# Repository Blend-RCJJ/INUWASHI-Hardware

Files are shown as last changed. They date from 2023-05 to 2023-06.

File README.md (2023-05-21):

# INUWASHI-Hardware

アートボード 1-100

2023 Bordeaux機 「INUWASHI」のハードウェアリポジトリ

## License 諸注意

CC-BY-NC-SA 4.0

- 商用利用不可
- 継承義務
- 改変可能

現役勢の皆様はルールの**ロボットはチームメンバー自身によって製作された物でなければならない。** に抵触しないようにご注意願います。（参考にしていただく分には歓迎です👌）

## 3D Data

私たちは機体の設計にAutodesk Fusion360を使用しています。機体の最新の設計データのリンクはこちらです。ダウンロードをご希望の方はTwitterのDMにて個別にお知らせください。

[https://a360.co/41CARyh](https://a360.co/41CARyh)

## フォルダ構成

- CFRP_DXF　カーボン発注のDXFファイル
- PCB　基板データ（Autodesk Eagle）
  - 01-main　メイン基板
  - 02-UI　UI基板
  - 03-ToF　距離センサ基板
  - 04-bottom　下段基板
  - 05-PWR　電源基板

## Topic

最近近くの伊吹山でいぬわしのひなが生まれたらしいです。ぴよぴよかわいいね！！

無題 - 2023年5月15日 22 13

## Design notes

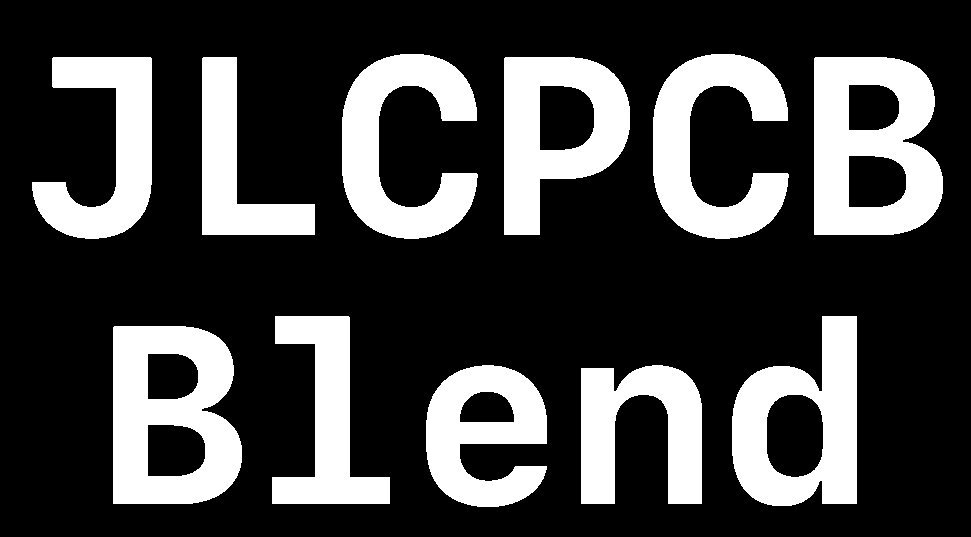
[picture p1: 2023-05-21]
PCB/03-ToF/top.bmp

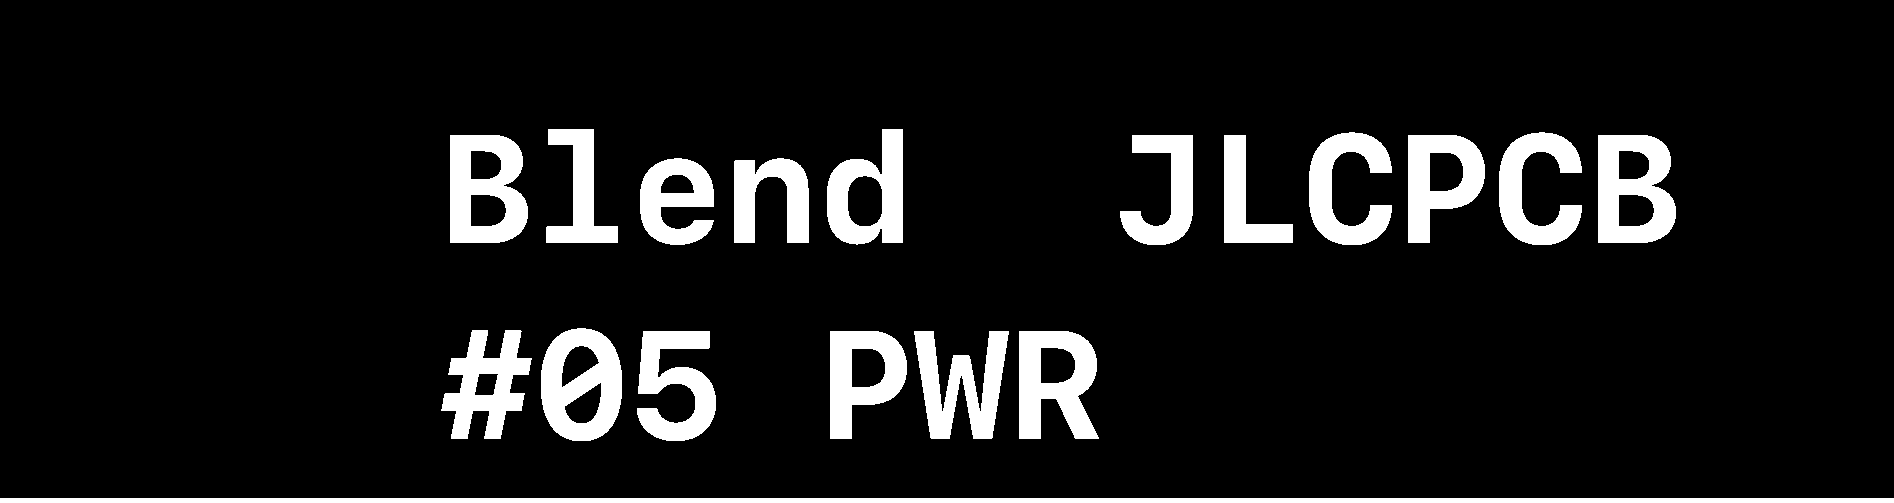
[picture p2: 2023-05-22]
PCB/05-PWR/アセット 2@5x.bmp

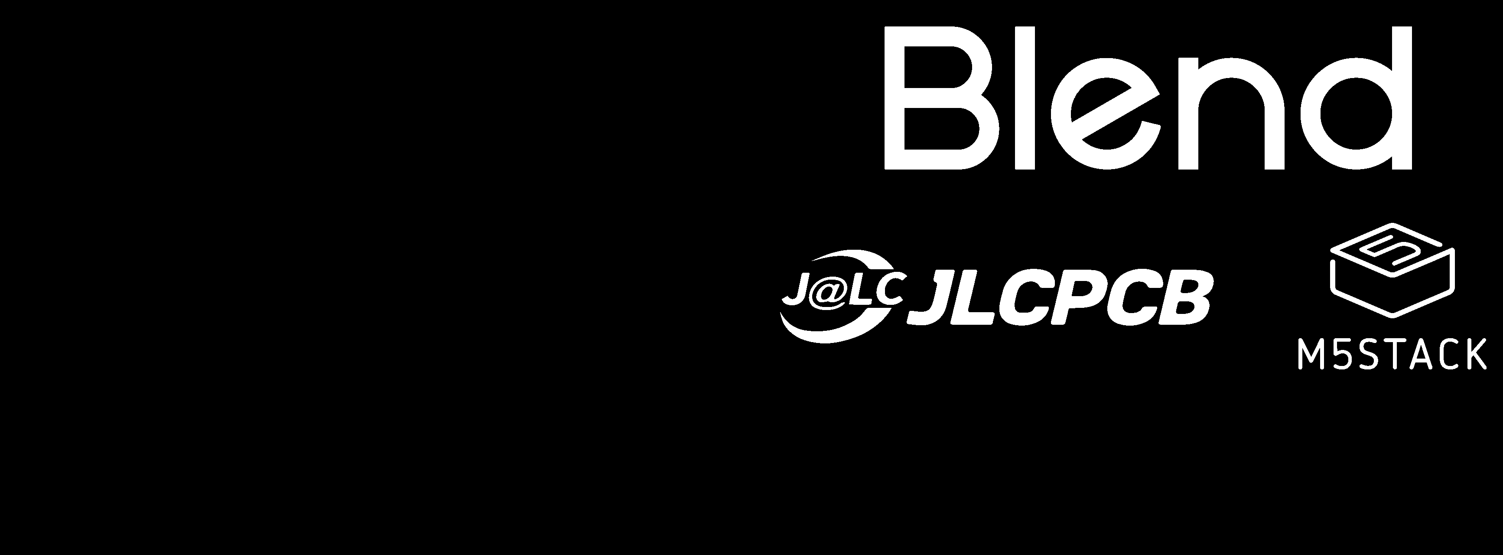
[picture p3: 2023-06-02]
PCB/01-main/アートボード 2@5x.bmp

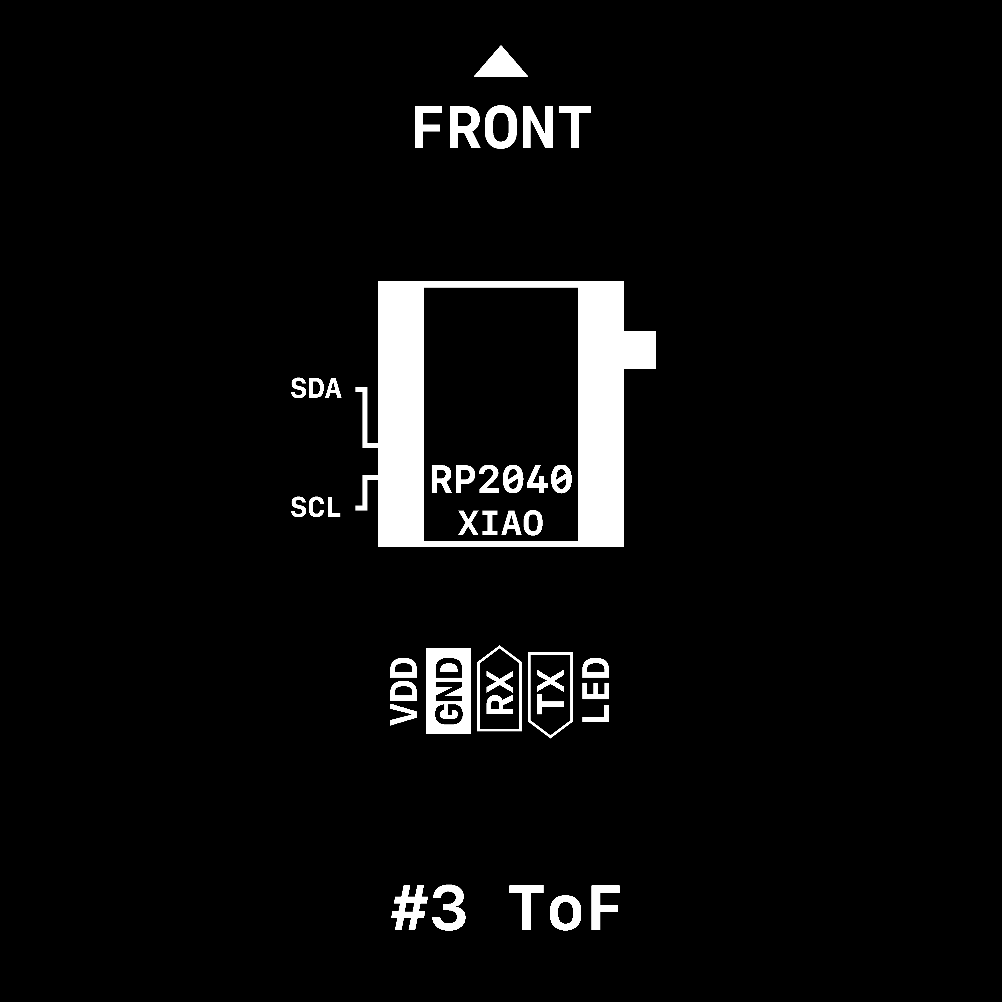
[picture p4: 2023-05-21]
PCB/03-ToF/bottom.bmp

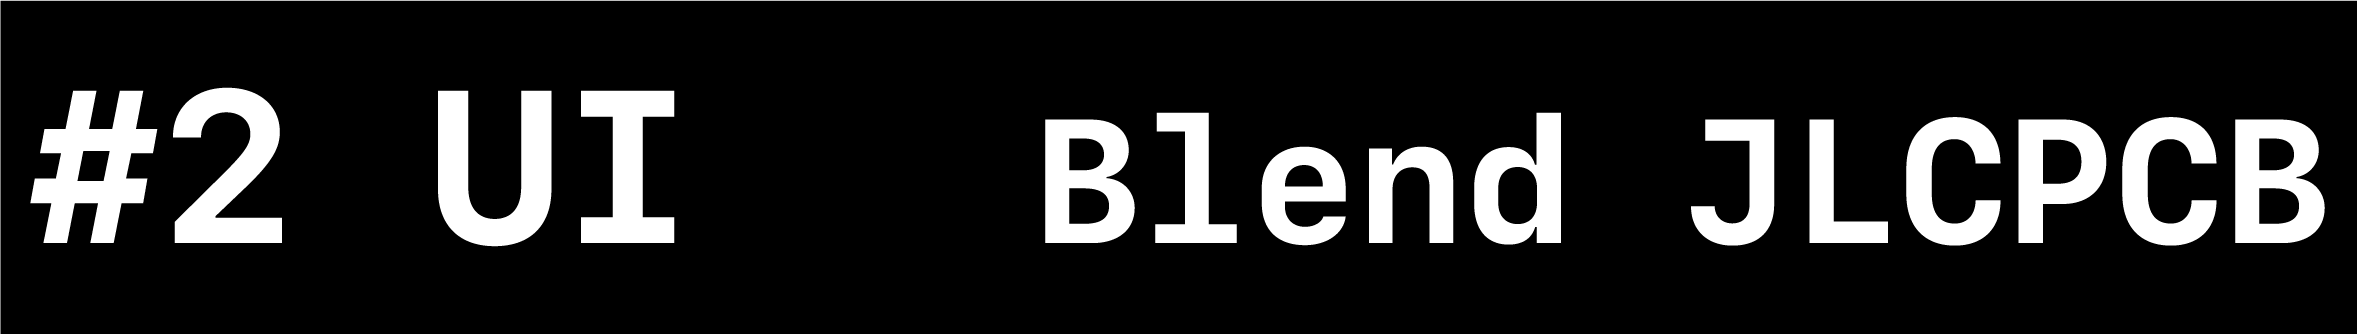
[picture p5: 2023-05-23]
PCB/02-UI/アセット 1@5x.png

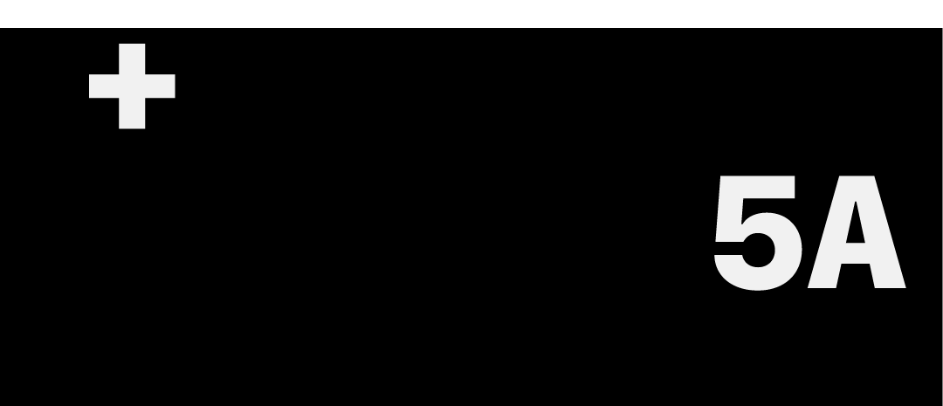
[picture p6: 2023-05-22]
PCB/05-PWR/アセット 1@5x.png

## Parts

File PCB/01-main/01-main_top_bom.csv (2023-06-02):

Comment | Designator | Footprint | LCSC Part #
0.1µ | C2 C3 C4 C5 C6 C7 C11 C14 C16 C18 | C0603 | C14663
1N4001 | D1 D2 D4 | SMA-DO214AC | C727079
1µ | C8 C17 C19 | C0603 | C15849
2k2 | R15 R16 | R0402 | C25879
4.7µ | C1 | C0603 | C19666
5k1 | R1 R2 | R0402 | C25879
7.5k | R17 | R0402 | C25918
10k | R4 R12 R13 R30 R31 | R0402 | C25744
20k | R14 | R0402 | C25765
100μ | C9 C13 C20 | 153CLV-0505 | C72487
270 | R3 R10 R32 | R0402 | C25099
BLUE | LED15 | SML0603 | C118339
BSS138 | T1 | SOT-23 | C112239
C1015 | Q1 | SOT23 | C181170
CH340ESMD | U1 | MSOP10 | C99652
MAX485ESA+T | U5 | SOIC127P600X175-8N | MAX485ED
MLT-8530 | LS1 | MLT-8530_JHE | C94599
STM32F446RET6 | U2 | LQFP64-10X10MM | C69336
WHITE | LED17 LED18 | SML0603 | C389521
WS2812B_2020 | LED1 LED2 LED3 LED4 LED5 LED6 LED7 LED8 LED9 LED10 LED11 LED12 LED13 LED14 | WS2812B_2020 | C965555
usb-c | X2 | USB_C_CUSB31-CFM2AX-01-X | C2987386

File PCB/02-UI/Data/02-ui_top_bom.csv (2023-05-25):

Comment | Designator | Footprint | LCSC Part #
WS2812B_2020 | LED1 LED2 LED3 LED4 LED5 LED6 LED7 LED8 LED9 LED10 LED11 LED12 LED13 LED14 | WS2812B_2020 | C965555

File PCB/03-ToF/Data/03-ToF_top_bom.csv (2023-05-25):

Comment | Designator | Footprint | LCSC Part #
0.1μ | C1 | C0402 | C285034
1N4007 | D1 | SMA-DO214AC | C727081
180 | R3 R4 | R0402 | C38941
1μ | C2 | C0402 | C52923
10k | R1 R2 R5 R6 R7 R8 R9 R10 R11 R12 R13 R14 R15 R16 R17 R18 R19 R20 R21 | R0402 | C269674
100μ | C3 C4 | 153CLV-0505 | C269674
BLUE | LED40 LED41 | SML0603 | C118339
NJM7805 | REG1 | MYPARTS_D-PAK_TO252AA
PCA9555PW 112 | U2 | SOP65P640X110-24N | C128392
WS2812B_5050N | LED1 LED2 LED3 LED4 LED5 LED6 LED7 LED8 LED9 LED10 LED11 LED12 LED13 LED14 LED15 LED16 LED17 LED18 LED19 LED20 LED21 LED22 LED23 LED24 LED25 LED26 LED27 LED28 LED29 LED30 LED31 LED32 | WS2812B-NARROW | C2874885

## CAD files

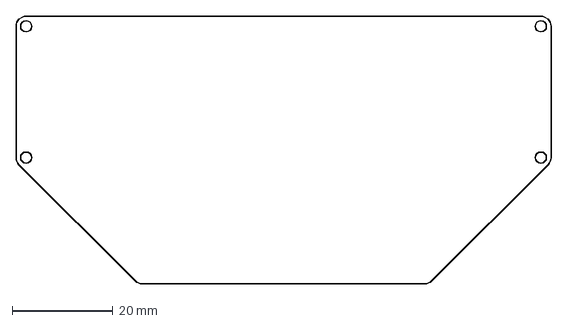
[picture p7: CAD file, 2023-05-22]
PCB/01-main/main.dxf
106.0 x 53.0 mm

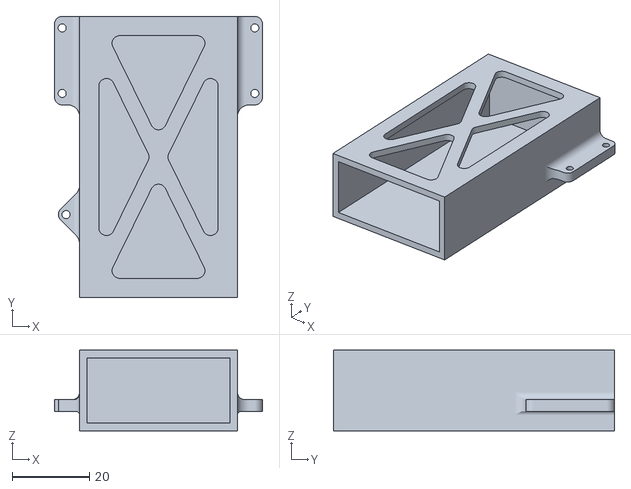
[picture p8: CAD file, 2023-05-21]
3D-Print/07-Battery-B-x4.stl
54.0 x 73.0 x 21.0

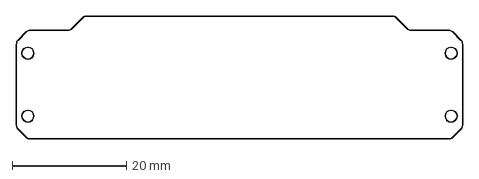
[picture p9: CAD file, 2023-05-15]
CFRP_DXF/02-patapata.dxf
78.0 x 21.5 mm

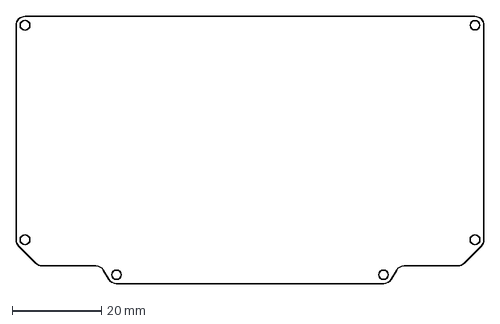
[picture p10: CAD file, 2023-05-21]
PCB/02-UI/02-ui.dxf
105.0 x 60.0 mm

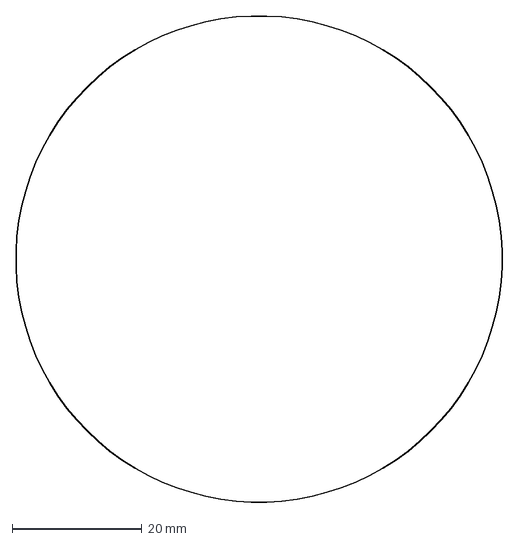
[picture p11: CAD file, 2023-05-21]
PCB/03-ToF/beta.dxf
75.0 x 75.0 mm

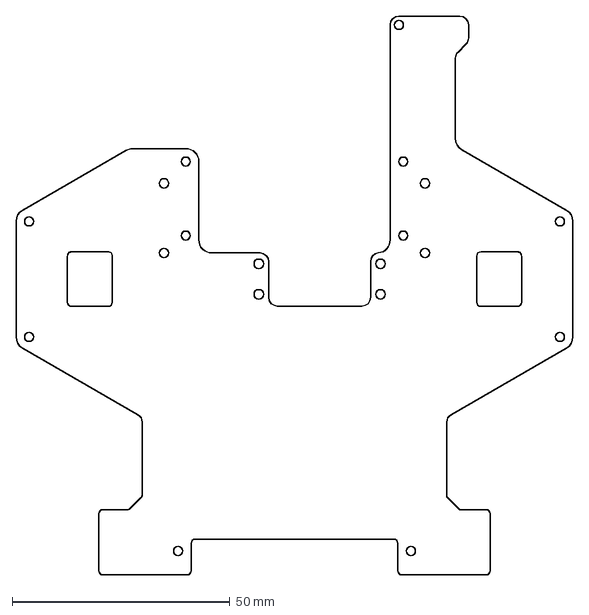
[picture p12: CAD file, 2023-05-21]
PCB/04-manta/04-bottom.dxf
128.0 x 128.5 mm

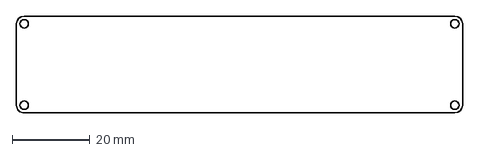
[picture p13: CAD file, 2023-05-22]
PCB/05-PWR/003-UI.dxf
115.0 x 25.0 mm

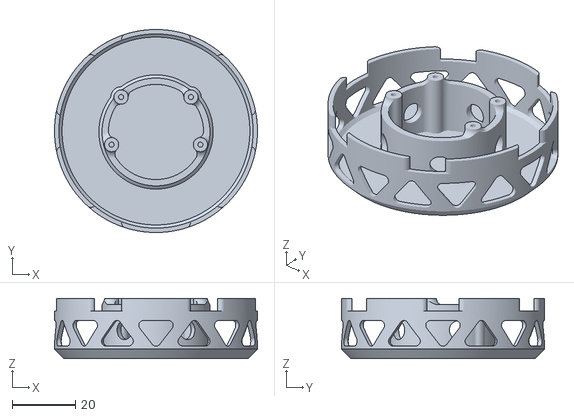
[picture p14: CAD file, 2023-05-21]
3D-Print/04-ToF-x3.stl
64.0 x 64.0 x 19.0

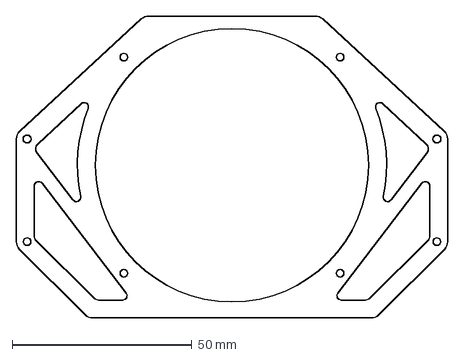
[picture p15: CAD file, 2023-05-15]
CFRP_DXF/01-top.dxf
120.0 x 84.0 mm

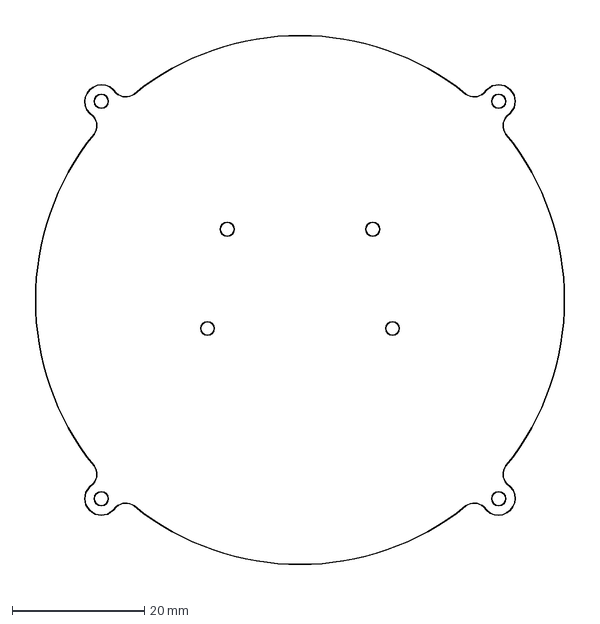
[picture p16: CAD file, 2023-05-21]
PCB/03-ToF/tof.dxf
85.9 x 85.9 mm

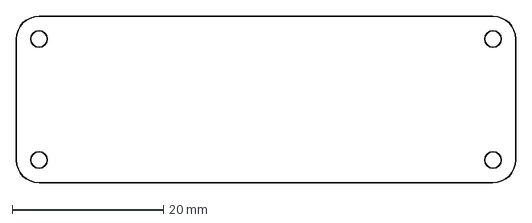
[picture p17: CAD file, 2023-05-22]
PCB/05-PWR/pwr.dxf
66.0 x 22.0 mm

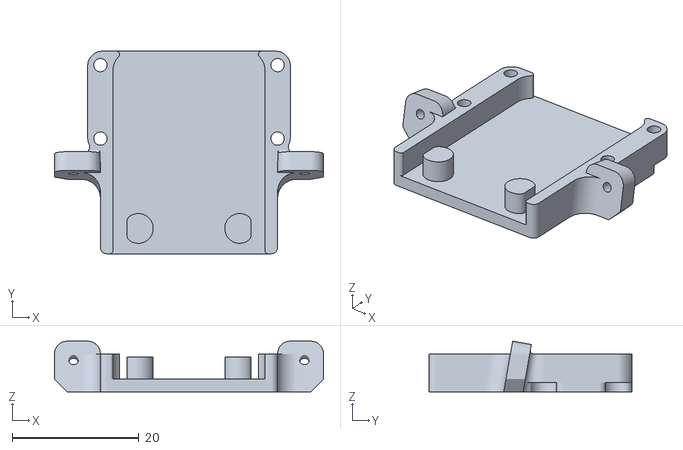
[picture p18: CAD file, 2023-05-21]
3D-Print/05-Camera-B-x6.stl
42.5 x 32.0 x 8.00

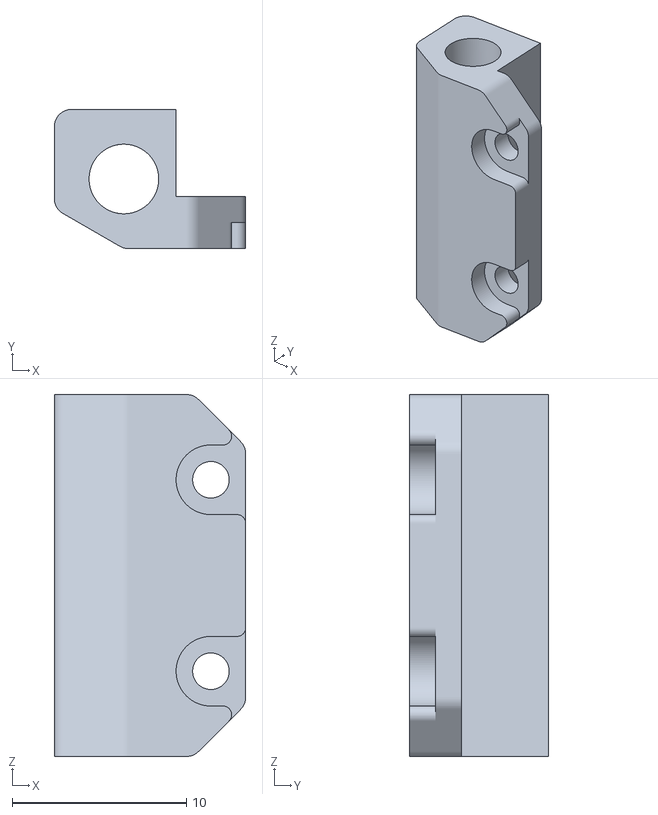
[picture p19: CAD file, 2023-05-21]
3D-Print/10-patapata-x4.stl
11.0 x 8.00 x 20.8

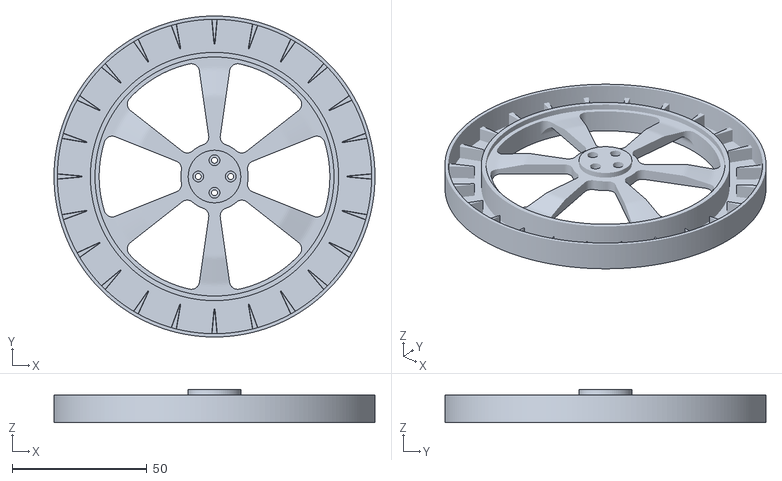
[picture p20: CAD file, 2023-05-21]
3D-Print/08-guruguru-x3.stl
119.0 x 119.0 x 12.3

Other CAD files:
3D-Print/06-Battery-A-x4.stl
3D-Print/02-Futa-A-x10.stl
3D-Print/04-Camera-A-x6.stl
3D-Print/08-guruguru-rev.2-x3.stl
3D-Print/01-Futa-B-x10.stl
3D-Print/09-gear-10.stl
3D-Print/09-gear-x10.stl

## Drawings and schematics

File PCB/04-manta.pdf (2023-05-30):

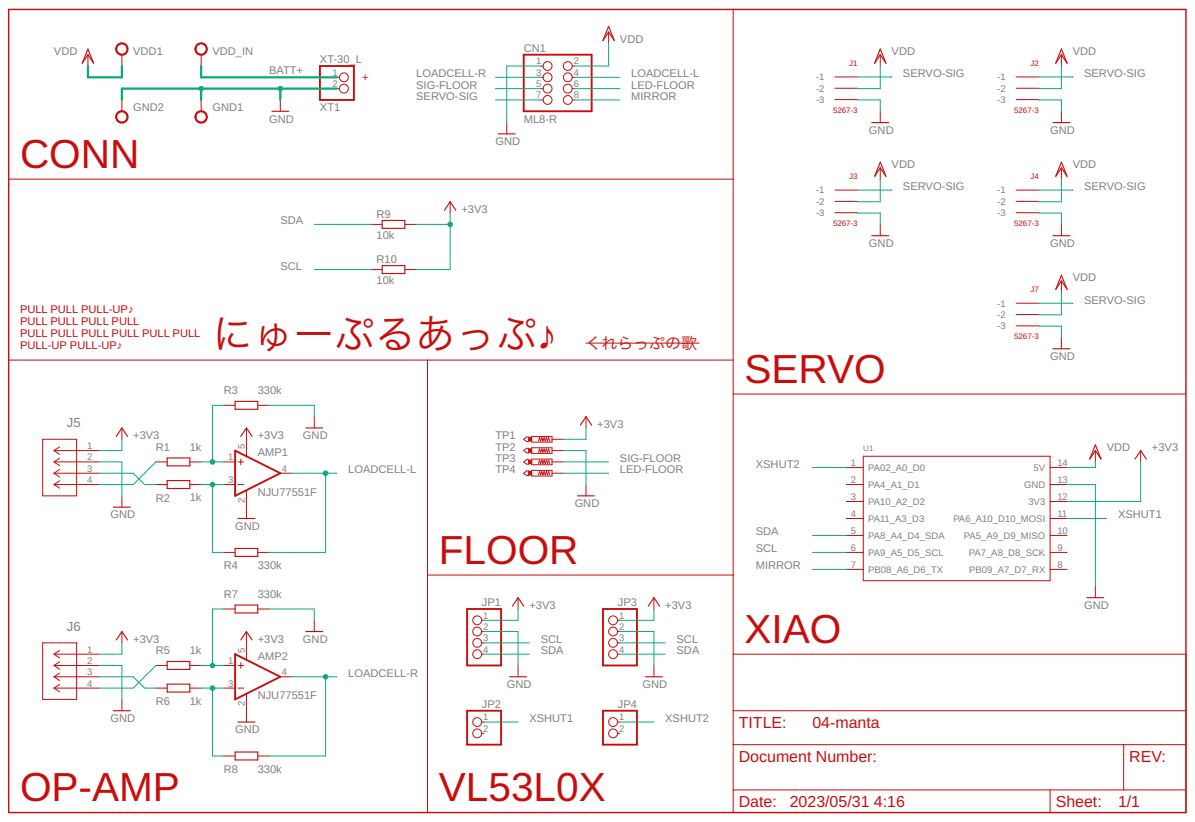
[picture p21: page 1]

CONN

PULL PULL PULL-UP♪ PULL PULL PULL PULL PULL PULL PULL PULL PULL PULL PULL-UP PULL-UP♪ | | くれらっぷの歌

R3 330k | TP2 GND FLOOR

Document Number: | REV:

Date: 2023/05/31 4:16 | Sheet: 1/1

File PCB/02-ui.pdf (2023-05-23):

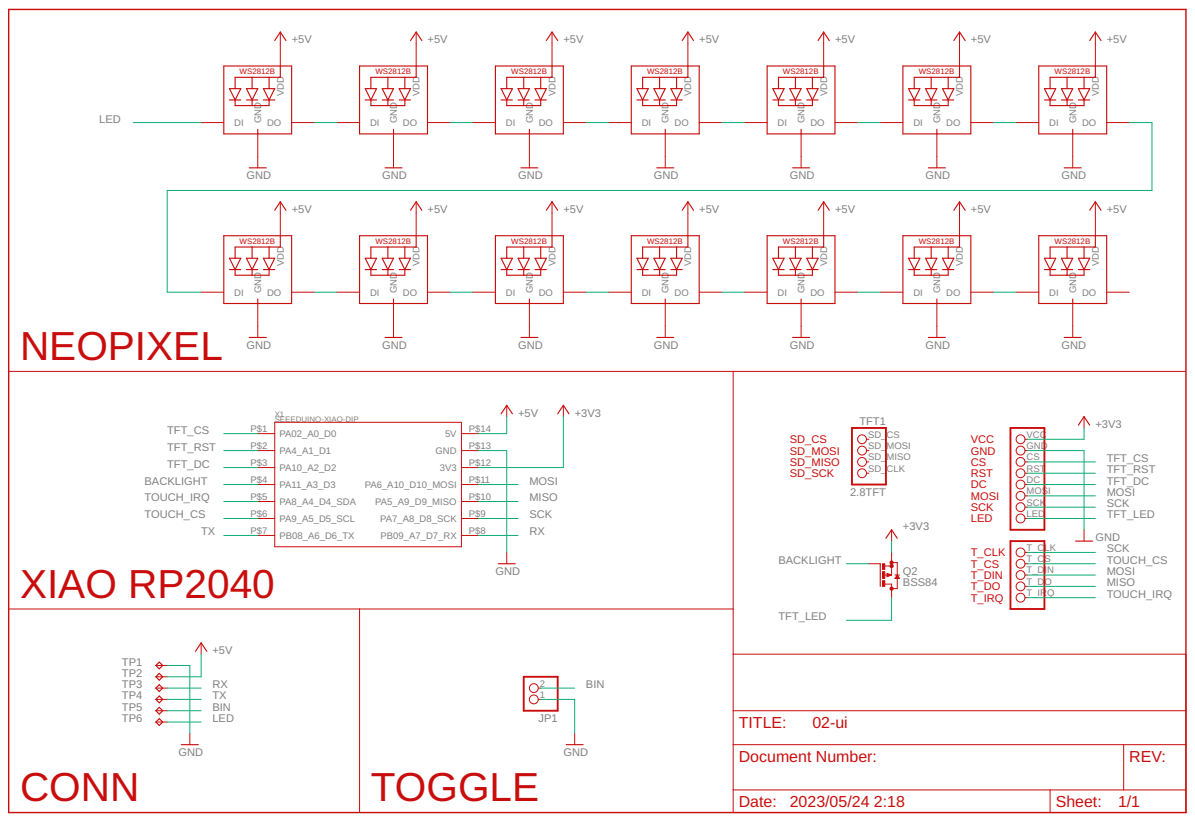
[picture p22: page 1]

XIAO RP2040 | GND

GND

Document Number: | REV:

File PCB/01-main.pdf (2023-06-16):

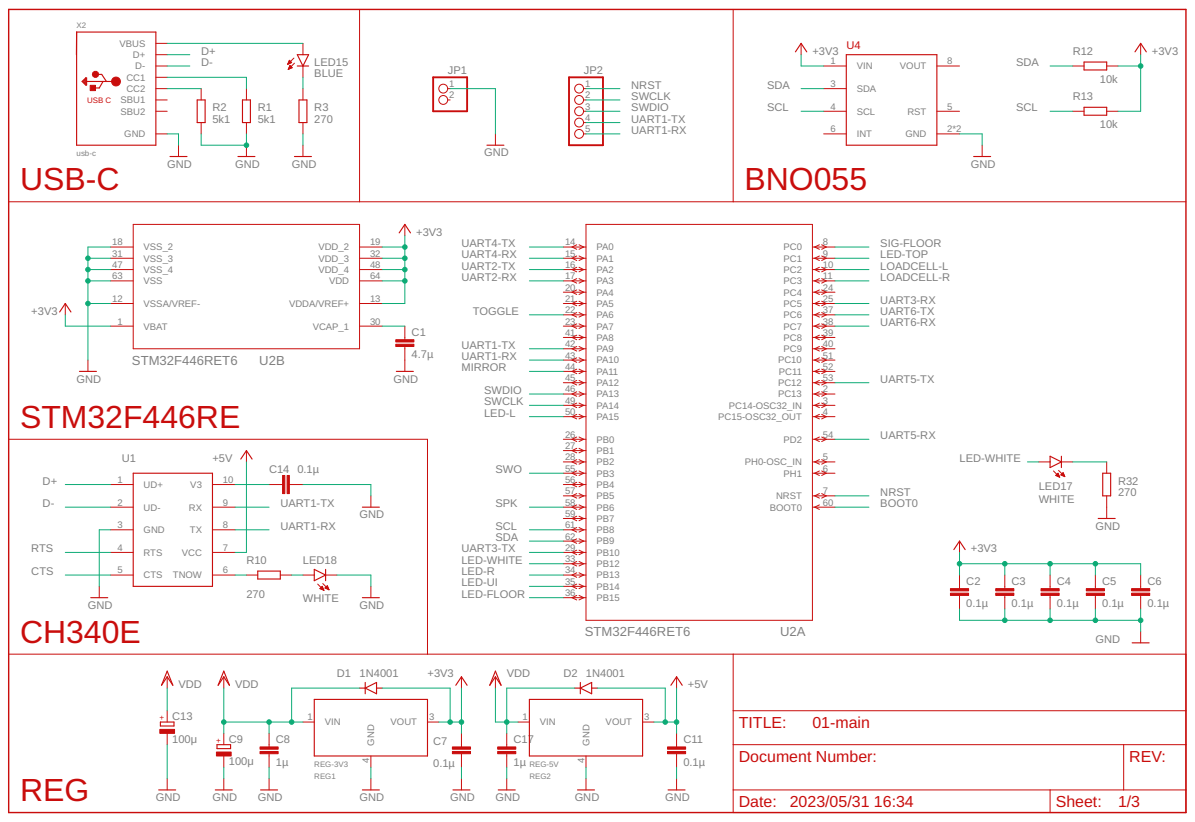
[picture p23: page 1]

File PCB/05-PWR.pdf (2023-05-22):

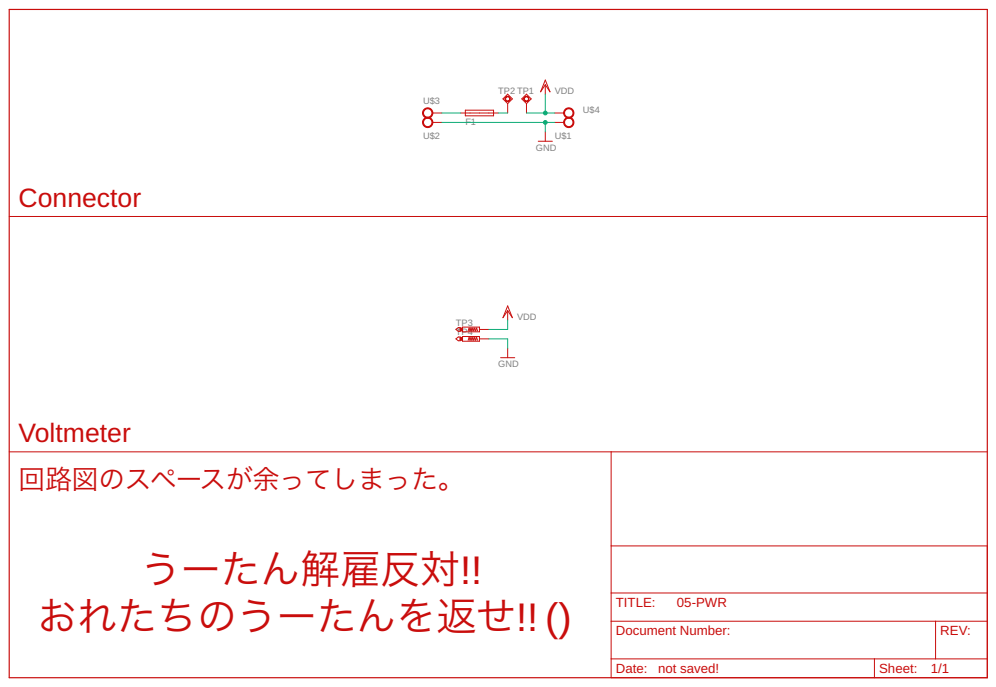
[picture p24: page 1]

回路図のスペースが余ってしまった。 うーたん解雇反対!! おれたちのうーたんを返せ!! ()

Document Number: | REV:

Date: not saved! | Sheet: 1/1

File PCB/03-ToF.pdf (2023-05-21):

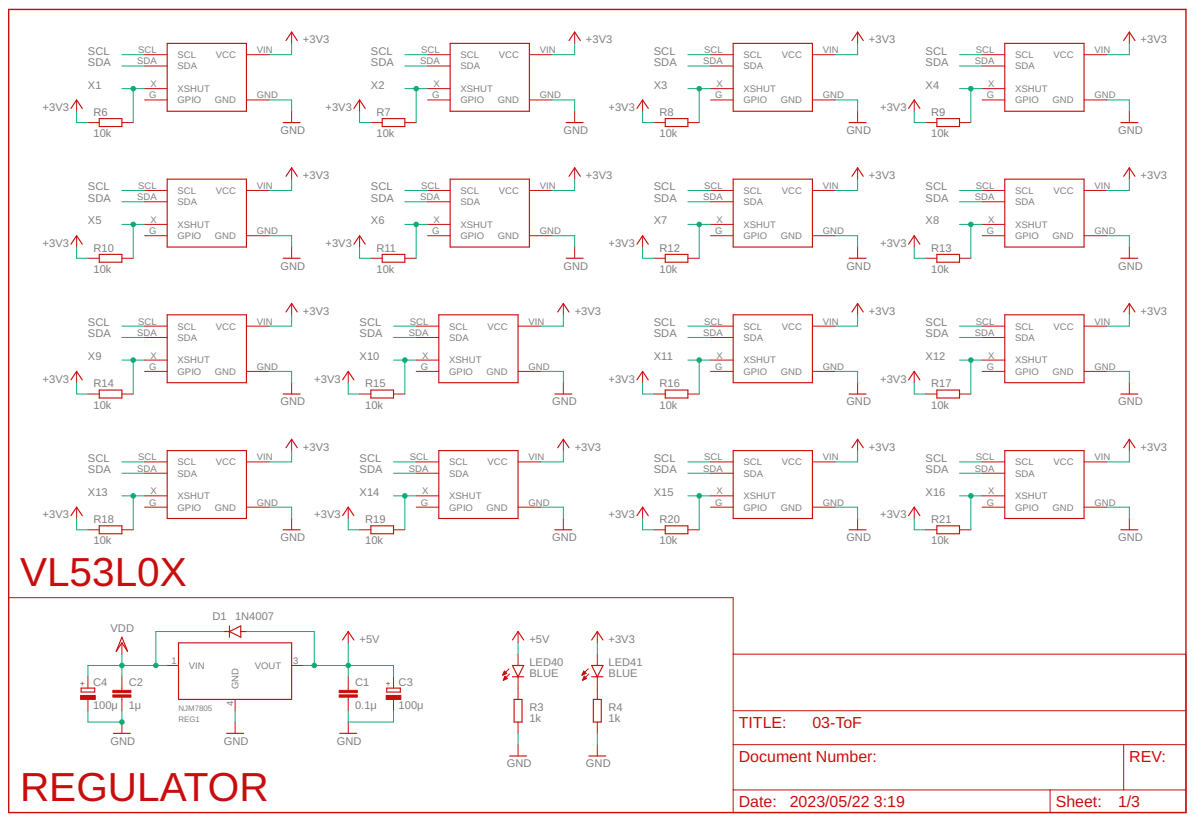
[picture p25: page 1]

Document Number: | REV:

Date: 2023/05/22 3:19 | Sheet: 1/3

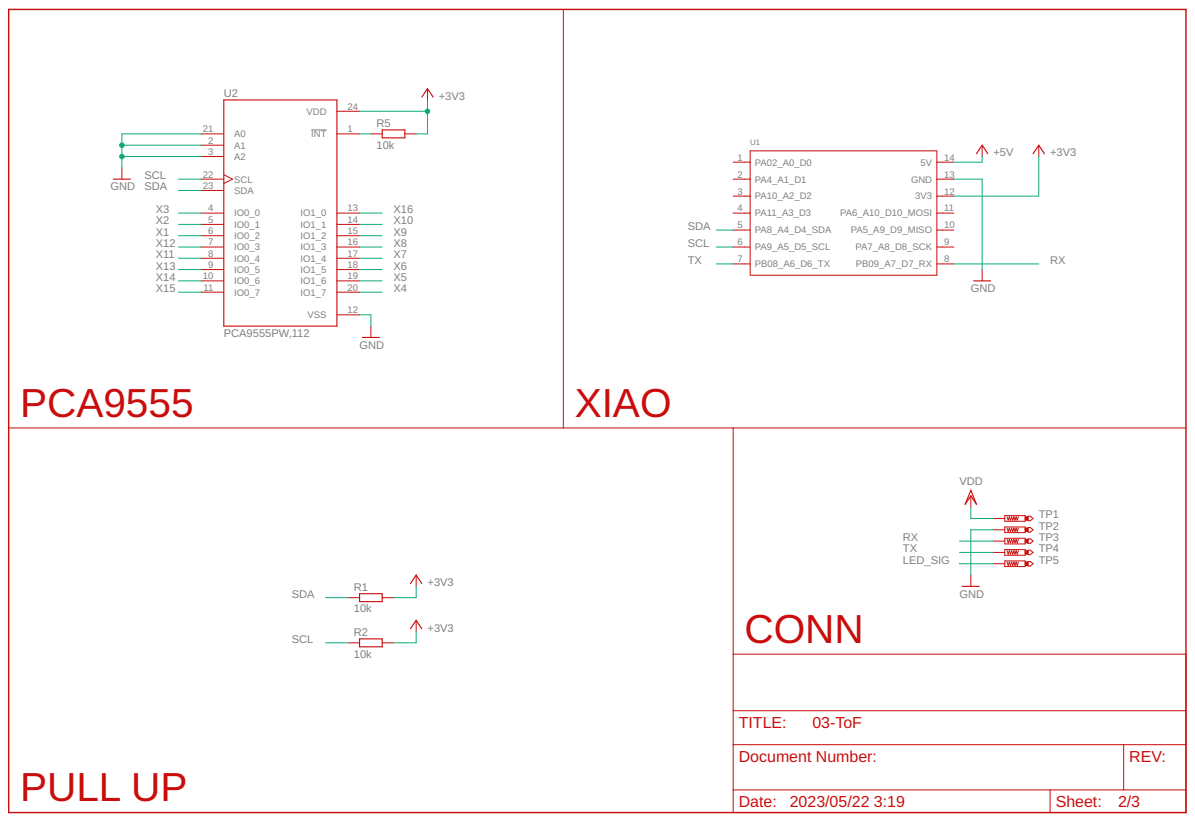
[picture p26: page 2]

Document Number: | REV:

Date: 2023/05/22 3:19 | Sheet: 2/3

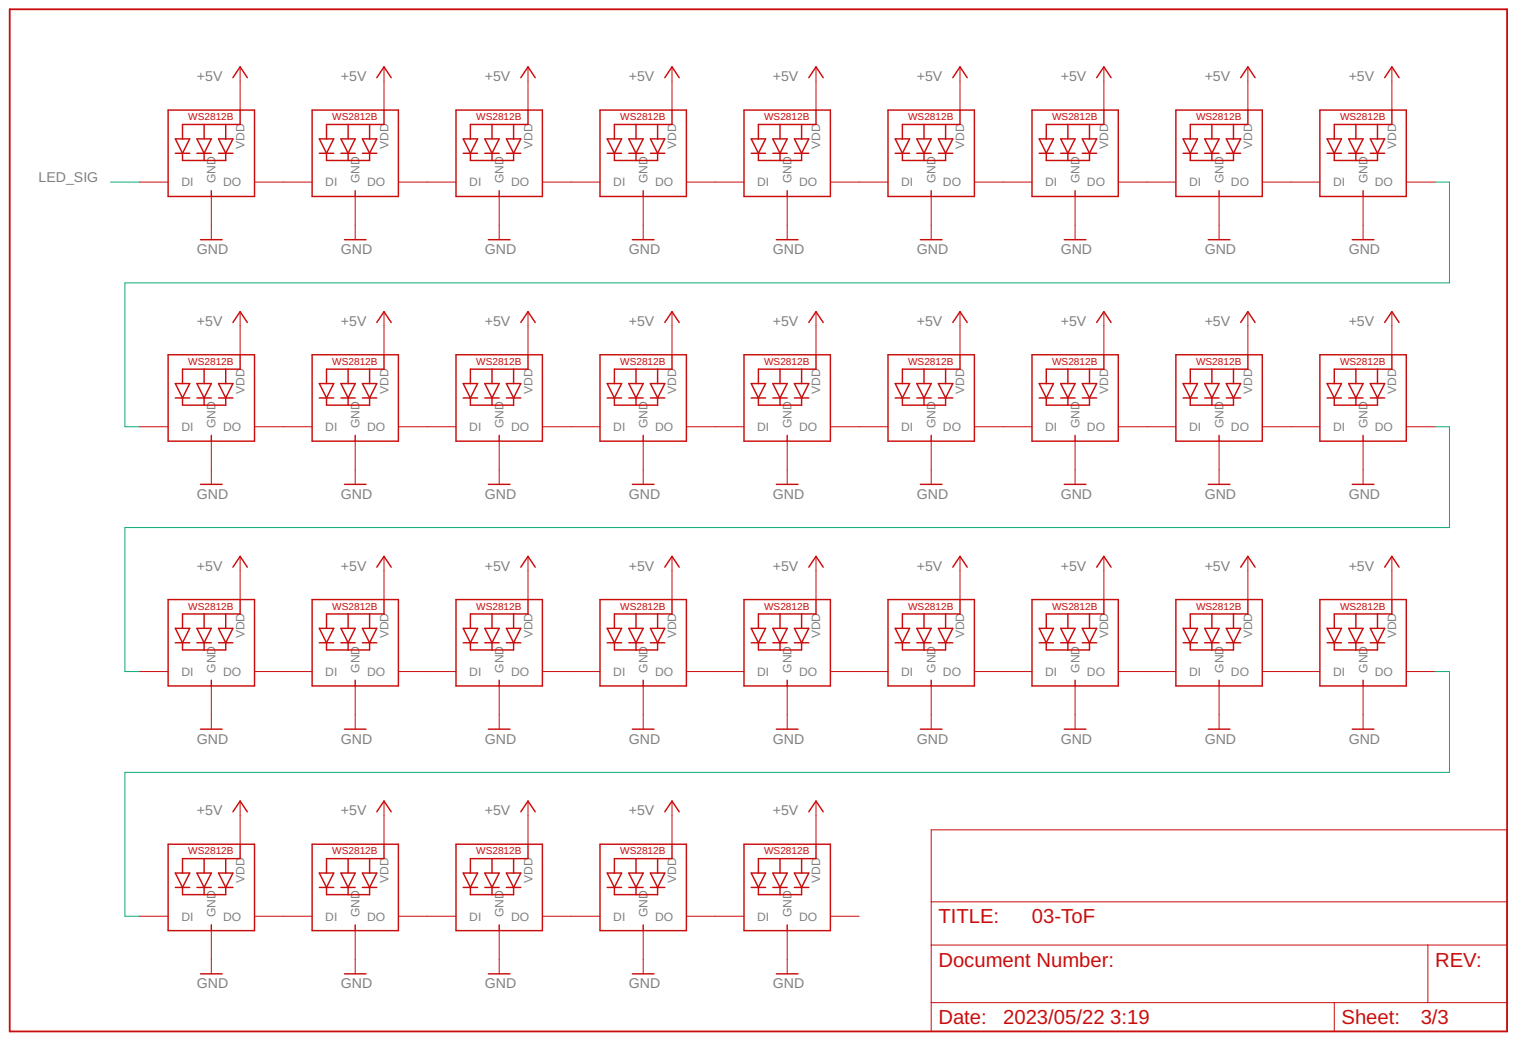
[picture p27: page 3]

Document Number: | REV:

Date: 2023/05/22 3:19 | Sheet: 3/3

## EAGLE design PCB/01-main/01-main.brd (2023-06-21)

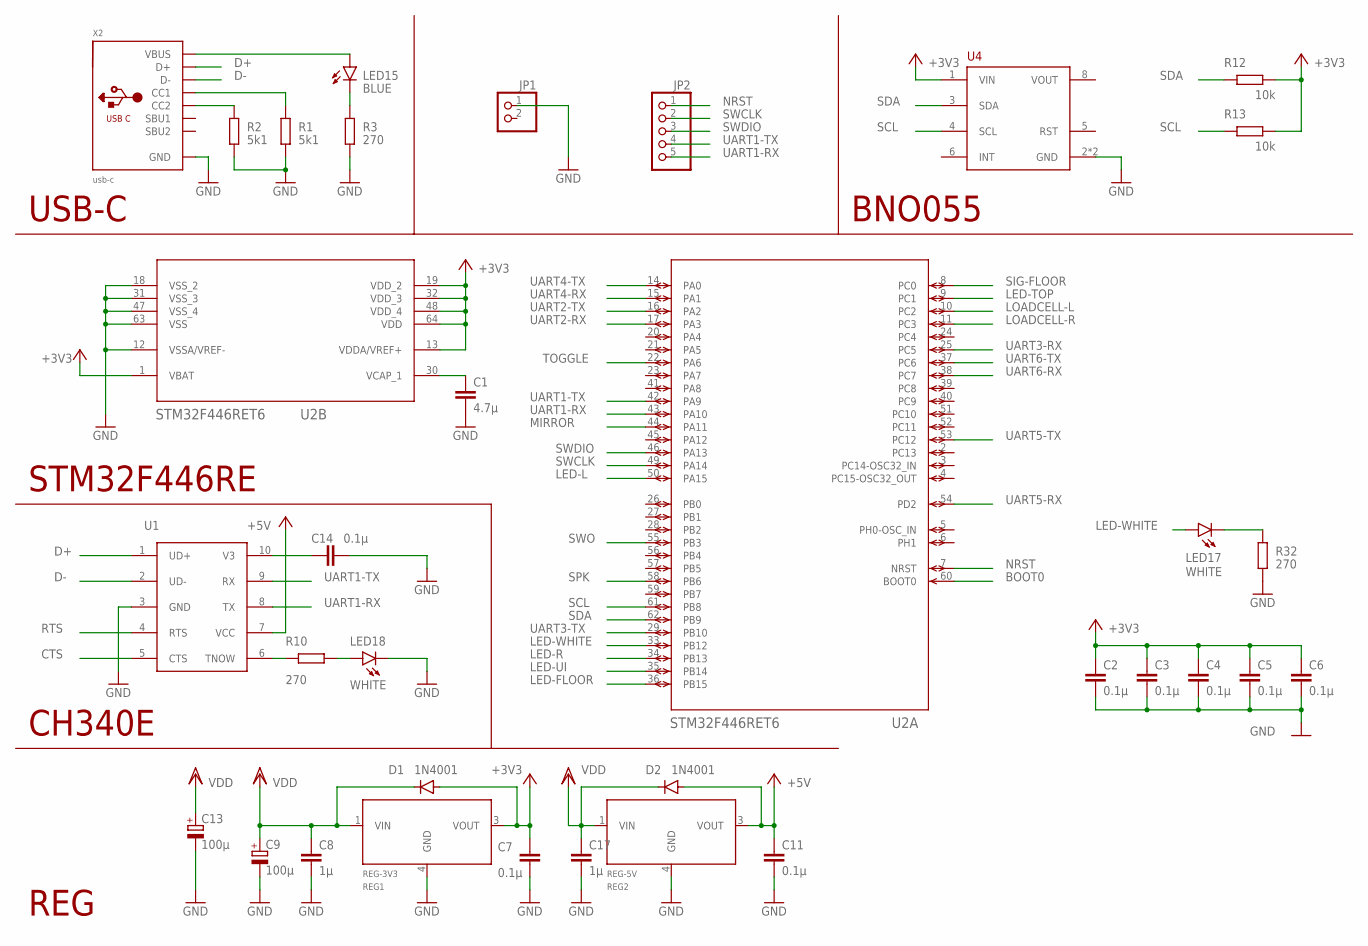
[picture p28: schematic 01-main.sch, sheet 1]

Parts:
C1: 4.7µ; C0603
C2, C3, C4, C5, C6, C7, C11, C14: 0.1µ; C0603
C8, C17: 1µ; C0603
C9, C13: 100μ; 153CLV-0505
D1, D2: 1N4001; SMA-DO214AC
JP1: PINHD-1X2; 1X02
JP2: PINHD-1X5; 1X05
LED15: BLUE; SML0603
LED17, LED18: WHITE; SML0603
R1, R2: 5k1; R0402
R3, R10, R32: 270; R0402
R12, R13: 10k; R0402
REG1: REG-3V3; MYPARTS_D-PAK_TO252AA
REG2: REG-5V; MYPARTS_D-PAK_TO252AA
U1: CH340ESMD; MSOP10
U2: STM32F446RET6; LQFP64-10X10MM
U4: BNO055; SOCKET-08
X2: usb-c; USB_C_CUSB31-CFM2AX-01-X

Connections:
+3V3: C2.1, C3.1, C4.1, C5.1, C6.1, C7.1, D1.A, R12.1, R13.1, REG1.3 (VOUT), U2.1 (VBAT), U2.13 (VDDA/VREF+), U2.19 (VDD_2), U2.32 (VDD_3), U2.48 (VDD_4), U2.64 (VDD), U4.1 (VIN); also elsewhere on the board
+5V: C11.1, D2.A, REG2.3 (VOUT), U1.7 (VCC); also elsewhere on the board
BOOT0: U2.60 (BOOT0); also elsewhere on the board
CTS: U1.5 (CTS)
D+: U1.1 (UD+), X2.A6 (D+), X2.B6 (D+)
D-: U1.2 (UD-), X2.A7 (D-), X2.B7 (D-)
GND: C1.2, C2.2, C3.2, C4.2, C5.2, C6.2, C7.2, C8.2, C9.-, C11.2, C13.-, C14.2, C17.2, JP1.1, LED18.C, R1.2, R2.2, R3.1, R32.1, REG1.4 (GND), REG2.4 (GND), U1.3 (GND), U2.12 (VSSA/VREF-), U2.18 (VSS_2), U2.31 (VSS_3), U2.47 (VSS_4), U2.63 (VSS), U4.2 (GND), U4.7 (GND), X2.A1B12 (GND), X2.B1A12 (GND); also elsewhere on the board
LED-FLOOR: U2.36 (PB15); also elsewhere on the board
LED-L: U2.50 (PA15); also elsewhere on the board
LED-R: U2.34 (PB13); also elsewhere on the board
LED-TOP: U2.9 (PC1); also elsewhere on the board
LED-UI: U2.35 (PB14); also elsewhere on the board
LED-WHITE: LED17.A, U2.33 (PB12)
LOADCELL-L: U2.10 (PC2); also elsewhere on the board
LOADCELL-R: U2.11 (PC3); also elsewhere on the board
MIRROR: U2.44 (PA11); also elsewhere on the board
unnamed: C14.1, U1.10 (V3)
unnamed: R1.1, X2.A5 (CC1)
unnamed: R2.1, X2.B5 (CC2)
unnamed: LED15.C, R3.2
unnamed: C1.1, U2.30 (VCAP_1)
unnamed: R10.2, U1.6 (TNOW)
unnamed: LED18.A, R10.1
unnamed: LED17.C, R32.2
unnamed: LED15.A, X2.A4B9 (VBUS), X2.B4A9 (VBUS)
NRST: JP2.1, U2.7 (NRST); also elsewhere on the board
RTS: U1.4 (RTS)
SCL: R13.2, U2.61 (PB8), U4.4 (SCL)
SDA: R12.2, U2.62 (PB9), U4.3 (SDA)
SIG-FLOOR: U2.8 (PC0); also elsewhere on the board
SPK: U2.58 (PB6); also elsewhere on the board
SWCLK: JP2.2, U2.49 (PA14)
SWDIO: JP2.3, U2.46 (PA13)
SWO: U2.55 (PB3)
TOGGLE: U2.22 (PA6); also elsewhere on the board
UART1-RX: JP2.5, U1.8 (TX), U2.43 (PA10)
UART1-TX: JP2.4, U1.9 (RX), U2.42 (PA9)
UART2-RX: U2.17 (PA3); also elsewhere on the board
UART2-TX: U2.16 (PA2); also elsewhere on the board
UART3-RX: U2.25 (PC5); also elsewhere on the board
UART3-TX: U2.29 (PB10); also elsewhere on the board
UART4-RX: U2.15 (PA1); also elsewhere on the board
UART4-TX: U2.14 (PA0); also elsewhere on the board
UART5-RX: U2.54 (PD2); also elsewhere on the board
UART5-TX: U2.53 (PC12); also elsewhere on the board
UART6-RX: U2.38 (PC7); also elsewhere on the board
UART6-TX: U2.37 (PC6); also elsewhere on the board
VDD: C8.1, C9.+, C13.+, C17.1, D1.K (C), D2.K (C), REG1.1 (VIN), REG2.1 (VIN); also elsewhere on the board
VOUT: U4.8 (VOUT)

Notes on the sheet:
STM32F446RE
REG
CH340E
USB-C
BNO055

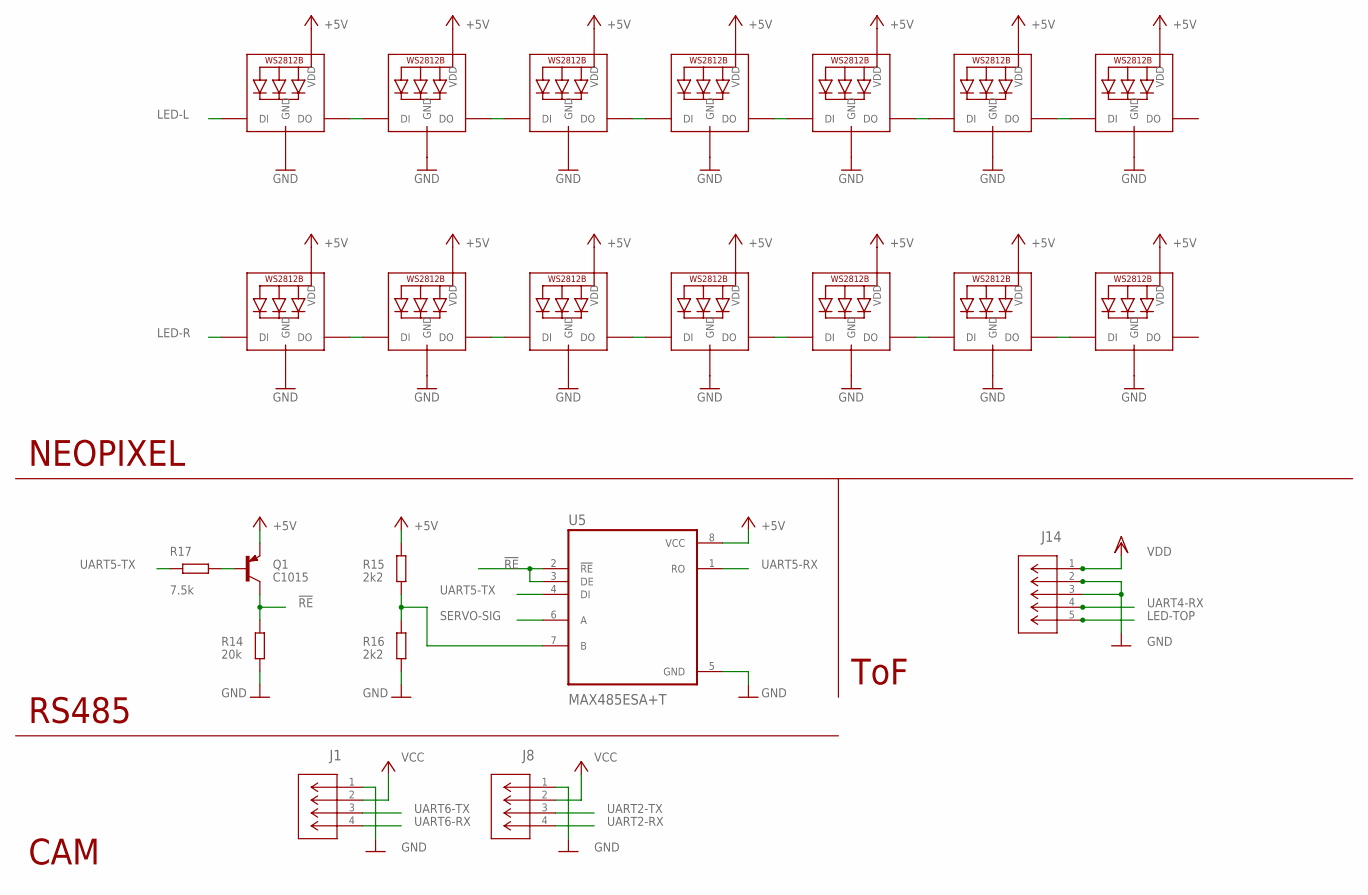
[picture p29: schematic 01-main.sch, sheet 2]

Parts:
J1, J8: 22057045; CON_22057045_MOL
J14: 22057055; CON_22057055_MOL
LED1, LED2, LED3, LED4, LED5, LED6, LED7, LED8, LED9, LED10, LED11, LED12, LED13, LED14: WS2812B_2020
Q1: C1015; SOT23
R14: 20k; R0402
R15, R16: 2k2; R0402
R17: 7.5k; R0402
U5: MAX485ESA+T; SOIC127P600X175-8N

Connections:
!RE: Q1.3 (C), R14.1, U5.2 (!RE), U5.3 (DE)
+5V: LED1.4 (VDD), LED2.4 (VDD), LED3.4 (VDD), LED4.4 (VDD), LED5.4 (VDD), LED6.4 (VDD), LED7.4 (VDD), LED8.4 (VDD), LED9.4 (VDD), LED10.4 (VDD), LED11.4 (VDD), LED12.4 (VDD), LED13.4 (VDD), LED14.4 (VDD), Q1.2 (E), R15.1, U5.8 (VCC); also elsewhere on the board
GND: J1.1, J8.1, J14.2, J14.3, LED1.2 (GND), LED2.2 (GND), LED3.2 (GND), LED4.2 (GND), LED5.2 (GND), LED6.2 (GND), LED7.2 (GND), LED8.2 (GND), LED9.2 (GND), LED10.2 (GND), LED11.2 (GND), LED12.2 (GND), LED13.2 (GND), LED14.2 (GND), R14.2, R16.2, U5.5 (GND); also elsewhere on the board
LED-L: LED1.3 (DI); also elsewhere on the board
LED-R: LED8.3 (DI); also elsewhere on the board
LED-TOP: J14.5; also elsewhere on the board
unnamed: LED1.1 (DO), LED2.3 (DI)
unnamed: LED2.1 (DO), LED3.3 (DI)
unnamed: LED3.1 (DO), LED4.3 (DI)
unnamed: LED4.1 (DO), LED5.3 (DI)
unnamed: LED5.1 (DO), LED6.3 (DI)
unnamed: LED6.1 (DO), LED7.3 (DI)
unnamed: LED8.1 (DO), LED9.3 (DI)
unnamed: LED9.1 (DO), LED10.3 (DI)
unnamed: LED10.1 (DO), LED11.3 (DI)
unnamed: LED11.1 (DO), LED12.3 (DI)
unnamed: LED12.1 (DO), LED13.3 (DI)
unnamed: LED13.1 (DO), LED14.3 (DI)
unnamed: Q1.1 (B), R17.1
unnamed: R15.2, R16.1, U5.7 (B)
SERVO-SIG: U5.6 (A); also elsewhere on the board
UART2-RX: J8.4; also elsewhere on the board
UART2-TX: J8.3; also elsewhere on the board
UART4-RX: J14.4; also elsewhere on the board
UART5-RX: U5.1 (RO); also elsewhere on the board
UART5-TX: R17.2, U5.4 (DI); also elsewhere on the board
UART6-RX: J1.4; also elsewhere on the board
UART6-TX: J1.3; also elsewhere on the board
VCC: J1.2, J8.2; also elsewhere on the board
VDD: J14.1; also elsewhere on the board

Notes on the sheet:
NEOPIXEL
ToF
CAM
RS485

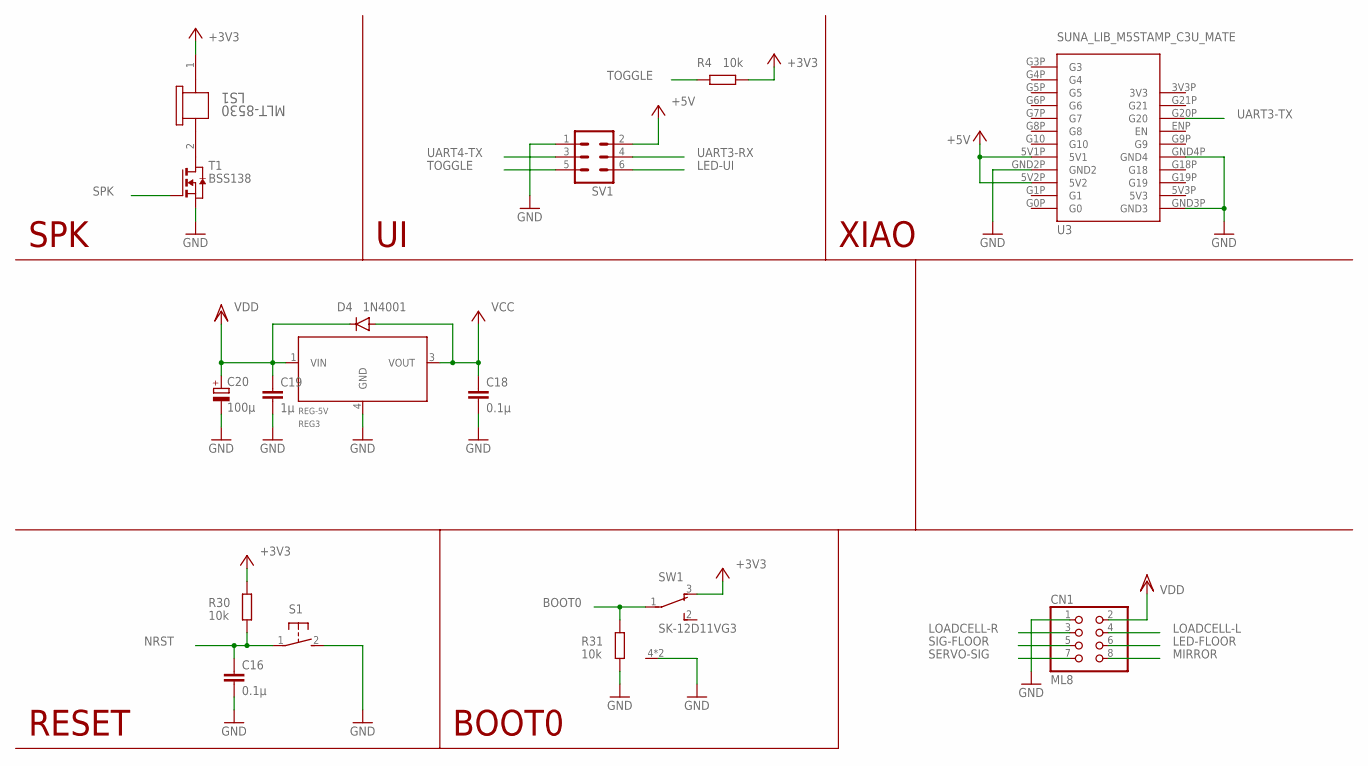
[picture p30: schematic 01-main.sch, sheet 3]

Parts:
C16, C18: 0.1µ; C0603
C19: 1µ; C0603
C20: 100μ; 153CLV-0505
CN1: ML8; ML6L
D4: 1N4001; SMA-DO214AC
LS1: MLT-8530; MLT-8530_JHE
R4, R30, R31: 10k; R0402
REG3: REG-5V; MYPARTS_D-PAK_TO252AA
S1: 31-XX; B3F-31XX
SV1: ML6L
SW1: SK-12D11VG3
T1: BSS138; SOT-23
U3: SUNA_LIB_M5STAMP_C3U_MATE; SUNA_LIB_M5STAMPC3UMATE

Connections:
+3V3: LS1.1, R4.1, R30.1, SW1.3 (O); also elsewhere on the board
+5V: SV1.2, U3.5V1P (5V1), U3.5V2P (5V2); also elsewhere on the board
BOOT0: R31.1, SW1.1; also elsewhere on the board
GND: C16.2, C18.2, C19.2, C20.-, CN1.1, R31.2, REG3.4 (GND), S1.2 (S), SV1.1, SW1.4 (CASE), SW1.5 (CASE), T1.2 (S), U3.GND2P (GND2), U3.GND3P (GND3), U3.GND4P (GND4); also elsewhere on the board
LED-FLOOR: CN1.6; also elsewhere on the board
LED-UI: SV1.6; also elsewhere on the board
LOADCELL-L: CN1.4; also elsewhere on the board
LOADCELL-R: CN1.3; also elsewhere on the board
MIRROR: CN1.8; also elsewhere on the board
unnamed: LS1.2, T1.1 (D)
NRST: C16.1, R30.2, S1.1; also elsewhere on the board
SERVO-SIG: CN1.7; also elsewhere on the board
SIG-FLOOR: CN1.5; also elsewhere on the board
SPK: T1.3 (G); also elsewhere on the board
TOGGLE: R4.2, SV1.5; also elsewhere on the board
UART3-RX: SV1.4; also elsewhere on the board
UART3-TX: U3.G20P (G20); also elsewhere on the board
UART4-TX: SV1.3; also elsewhere on the board
VCC: C18.1, D4.A, REG3.3 (VOUT); also elsewhere on the board
VDD: C19.1, C20.+, CN1.2, D4.K (C), REG3.1 (VIN); also elsewhere on the board

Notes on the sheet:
XIAO
SPK
RESET
BOOT0

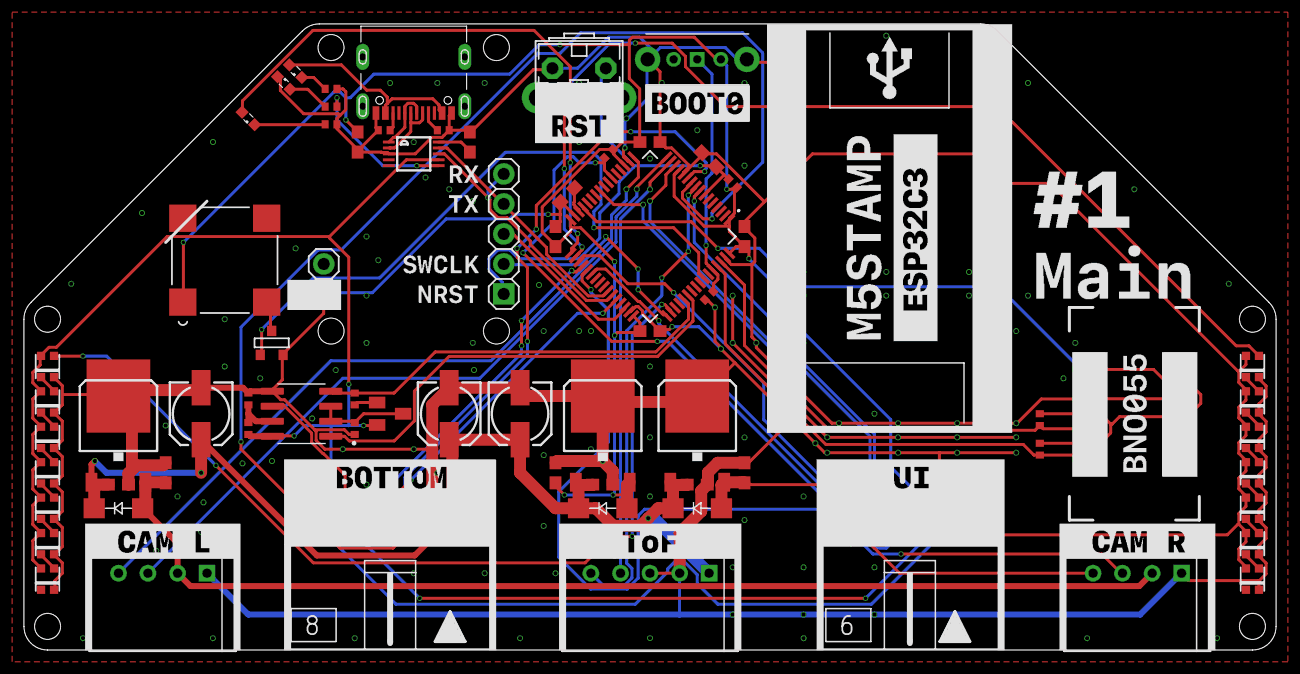
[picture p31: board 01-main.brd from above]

Board: 2 copper layers, 106.0 x 53.0 mm, 72 parts (0 on the bottom side), 63 nets.

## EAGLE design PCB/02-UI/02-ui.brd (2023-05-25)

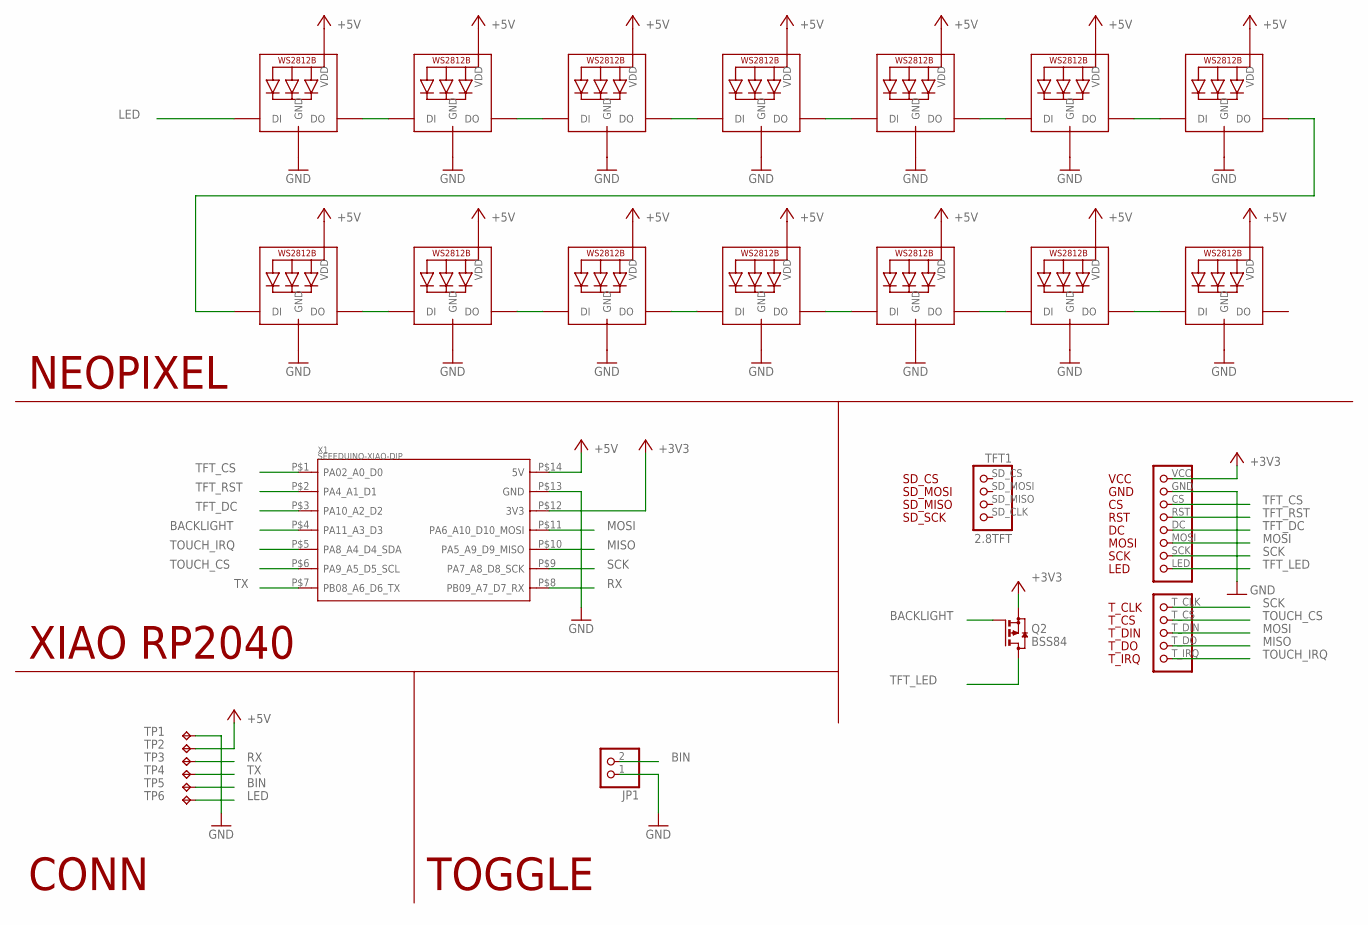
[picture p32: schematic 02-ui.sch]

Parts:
JP1: PINHD-1X2; 1X02
LED1, LED2, LED3, LED4, LED5, LED6, LED7, LED8, LED9, LED10, LED11, LED12, LED13, LED14: WS2812B_2020
Q2: BSS84; SOT23
TFT1: 2.8TFT
TP1: TPTP10SQ; TP10SQ
TP2, TP3, TP4, TP5, TP6: TPTP10R; TP10R
X1: SEEEDUINO-XIAO-DIP; XIAO-PINHEAD

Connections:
+3V3: Q2.2 (S), TFT1.VCC, X1.P$12 (3V3)
+5V: LED1.4 (VDD), LED2.4 (VDD), LED3.4 (VDD), LED4.4 (VDD), LED5.4 (VDD), LED6.4 (VDD), LED7.4 (VDD), LED8.4 (VDD), LED9.4 (VDD), LED10.4 (VDD), LED11.4 (VDD), LED12.4 (VDD), LED13.4 (VDD), LED14.4 (VDD), TP2.TP, X1.P$14 (5V)
BACKLIGHT: Q2.1 (G), X1.P$4 (PA11_A3_D3)
BIN: JP1.2, TP5.TP
GND: JP1.1, LED1.2 (GND), LED2.2 (GND), LED3.2 (GND), LED4.2 (GND), LED5.2 (GND), LED6.2 (GND), LED7.2 (GND), LED8.2 (GND), LED9.2 (GND), LED10.2 (GND), LED11.2 (GND), LED12.2 (GND), LED13.2 (GND), LED14.2 (GND), TFT1.GND, TP1.TP, X1.P$13 (GND)
LED: LED1.3 (DI), TP6.TP
MISO: TFT1.T_DO, X1.P$10 (PA5_A9_D9_MISO)
MOSI: TFT1.MOSI, TFT1.T_DIN, X1.P$11 (PA6_A10_D10_MOSI)
unnamed: LED1.1 (DO), LED2.3 (DI)
unnamed: LED2.1 (DO), LED3.3 (DI)
unnamed: LED3.1 (DO), LED4.3 (DI)
unnamed: LED4.1 (DO), LED5.3 (DI)
unnamed: LED6.1 (DO), LED7.3 (DI)
unnamed: LED10.1 (DO), LED11.3 (DI)
unnamed: LED8.1 (DO), LED9.3 (DI)
unnamed: LED9.1 (DO), LED10.3 (DI)
unnamed: LED5.1 (DO), LED6.3 (DI)
unnamed: LED11.1 (DO), LED12.3 (DI)
unnamed: LED12.1 (DO), LED13.3 (DI)
unnamed: LED13.1 (DO), LED14.3 (DI)
unnamed: LED7.1 (DO), LED8.3 (DI)
RX: TP3.TP, X1.P$8 (PB09_A7_D7_RX)
SCK: TFT1.SCK, TFT1.T_CLK, X1.P$9 (PA7_A8_D8_SCK)
TFT_CS: TFT1.CS, X1.P$1 (PA02_A0_D0)
TFT_DC: TFT1.DC, X1.P$3 (PA10_A2_D2)
TFT_LED: Q2.3 (D), TFT1.LED
TFT_RST: TFT1.RST, X1.P$2 (PA4_A1_D1)
TOUCH_CS: TFT1.T_CS, X1.P$6 (PA9_A5_D5_SCL)
TOUCH_IRQ: TFT1.T_IRQ, X1.P$5 (PA8_A4_D4_SDA)
TX: TP4.TP, X1.P$7 (PB08_A6_D6_TX)

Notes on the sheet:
NEOPIXEL
XIAO RP2040
CONN
TOGGLE

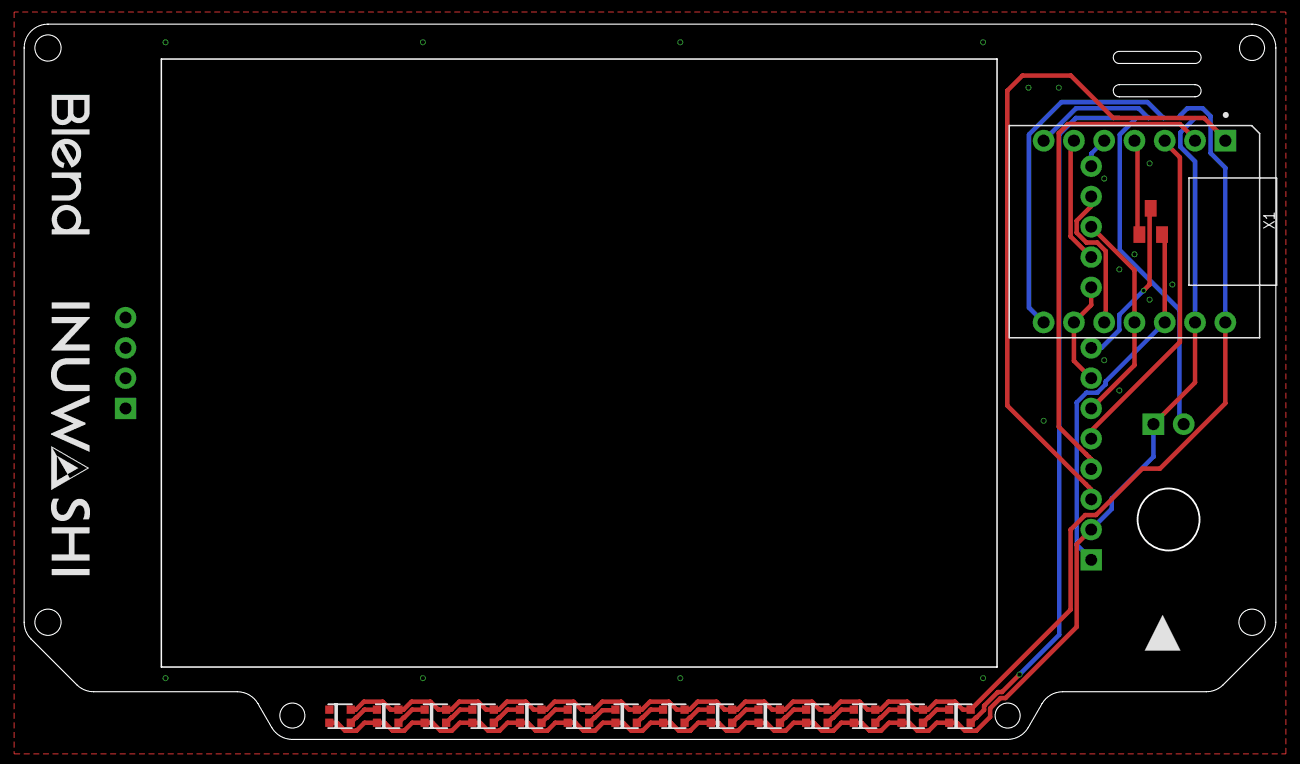
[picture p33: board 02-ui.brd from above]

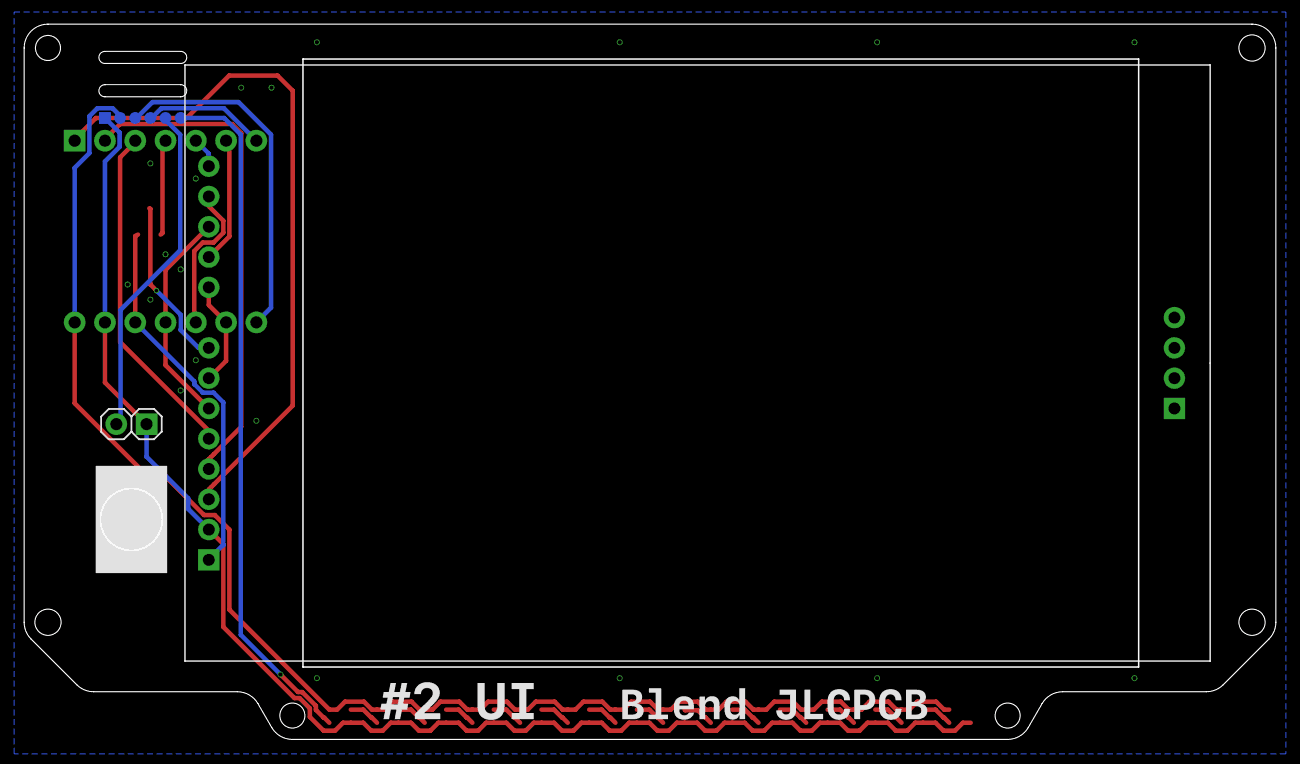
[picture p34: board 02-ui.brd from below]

Board: 2 copper layers, 105.0 x 60.0 mm, 24 parts (7 on the bottom side), 30 nets.

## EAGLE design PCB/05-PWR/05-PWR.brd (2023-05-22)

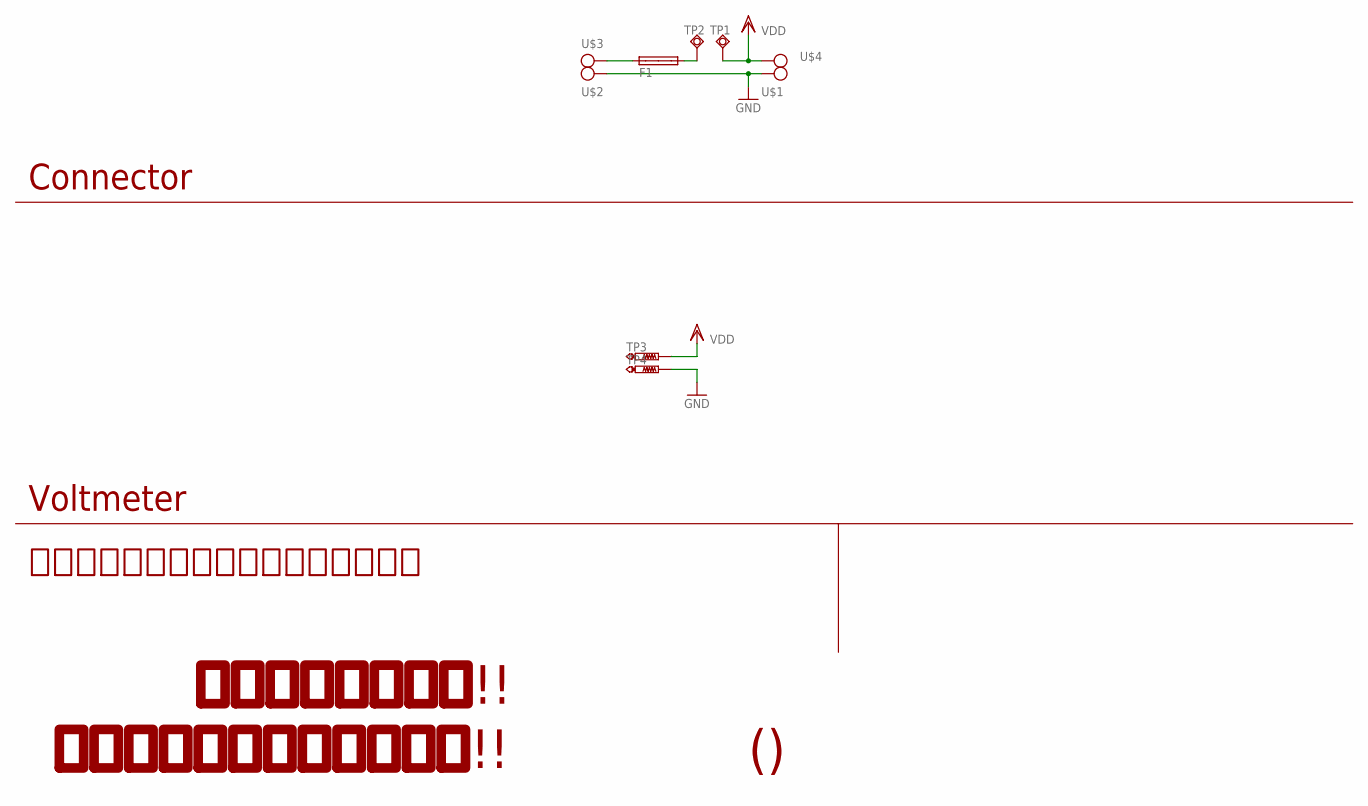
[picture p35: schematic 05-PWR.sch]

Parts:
F1: SHK20L
TP1, TP2: TPSQPAD1-20; P1-20
TP3: PTR1TP15R; TP15R
TP4: PTR1TP15SQ; TP15SQ
U$1, U$2, U$3, U$4: PAD_VDD; VDD

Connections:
GND: TP4.TP, U$1.P$1, U$2.P$1
unnamed: F1.1A, U$3.P$1
unnamed: F1.2A, TP2.TP
VDD: TP1.TP, TP3.TP, U$4.P$1

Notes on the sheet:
Connector
Voltmeter
回路図のスペースが余ってしまった。
うーたん解雇反対!!
おれたちのうーたんを返せ!!

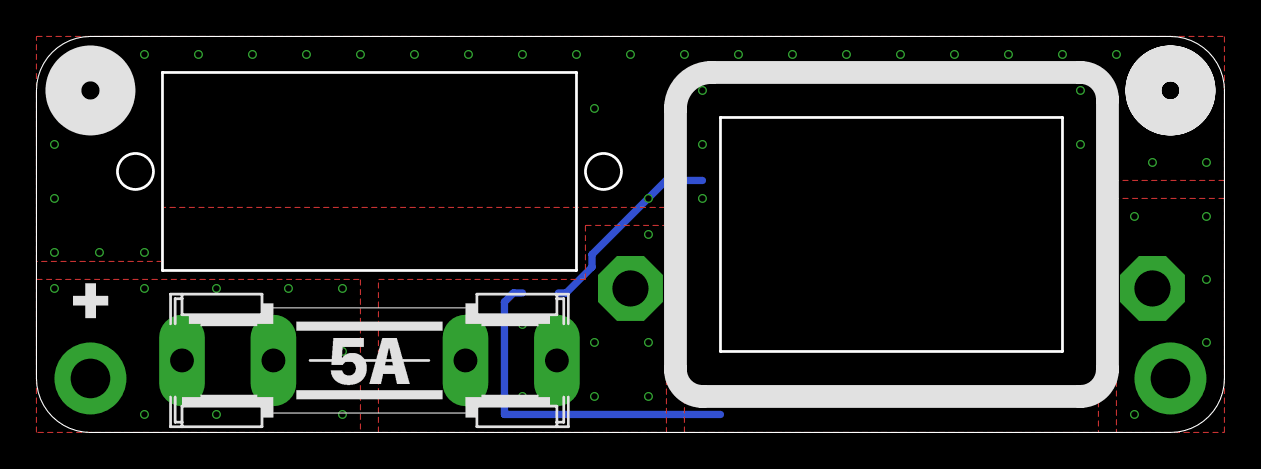
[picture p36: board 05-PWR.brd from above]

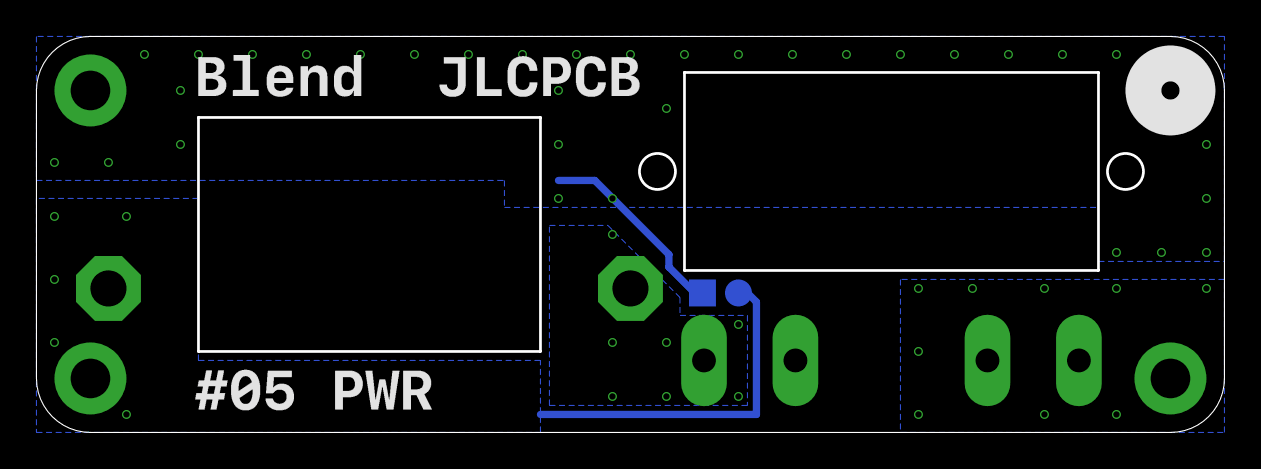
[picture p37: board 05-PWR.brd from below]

Board: 2 copper layers, 66.0 x 22.0 mm, 9 parts (2 on the bottom side), 4 nets.

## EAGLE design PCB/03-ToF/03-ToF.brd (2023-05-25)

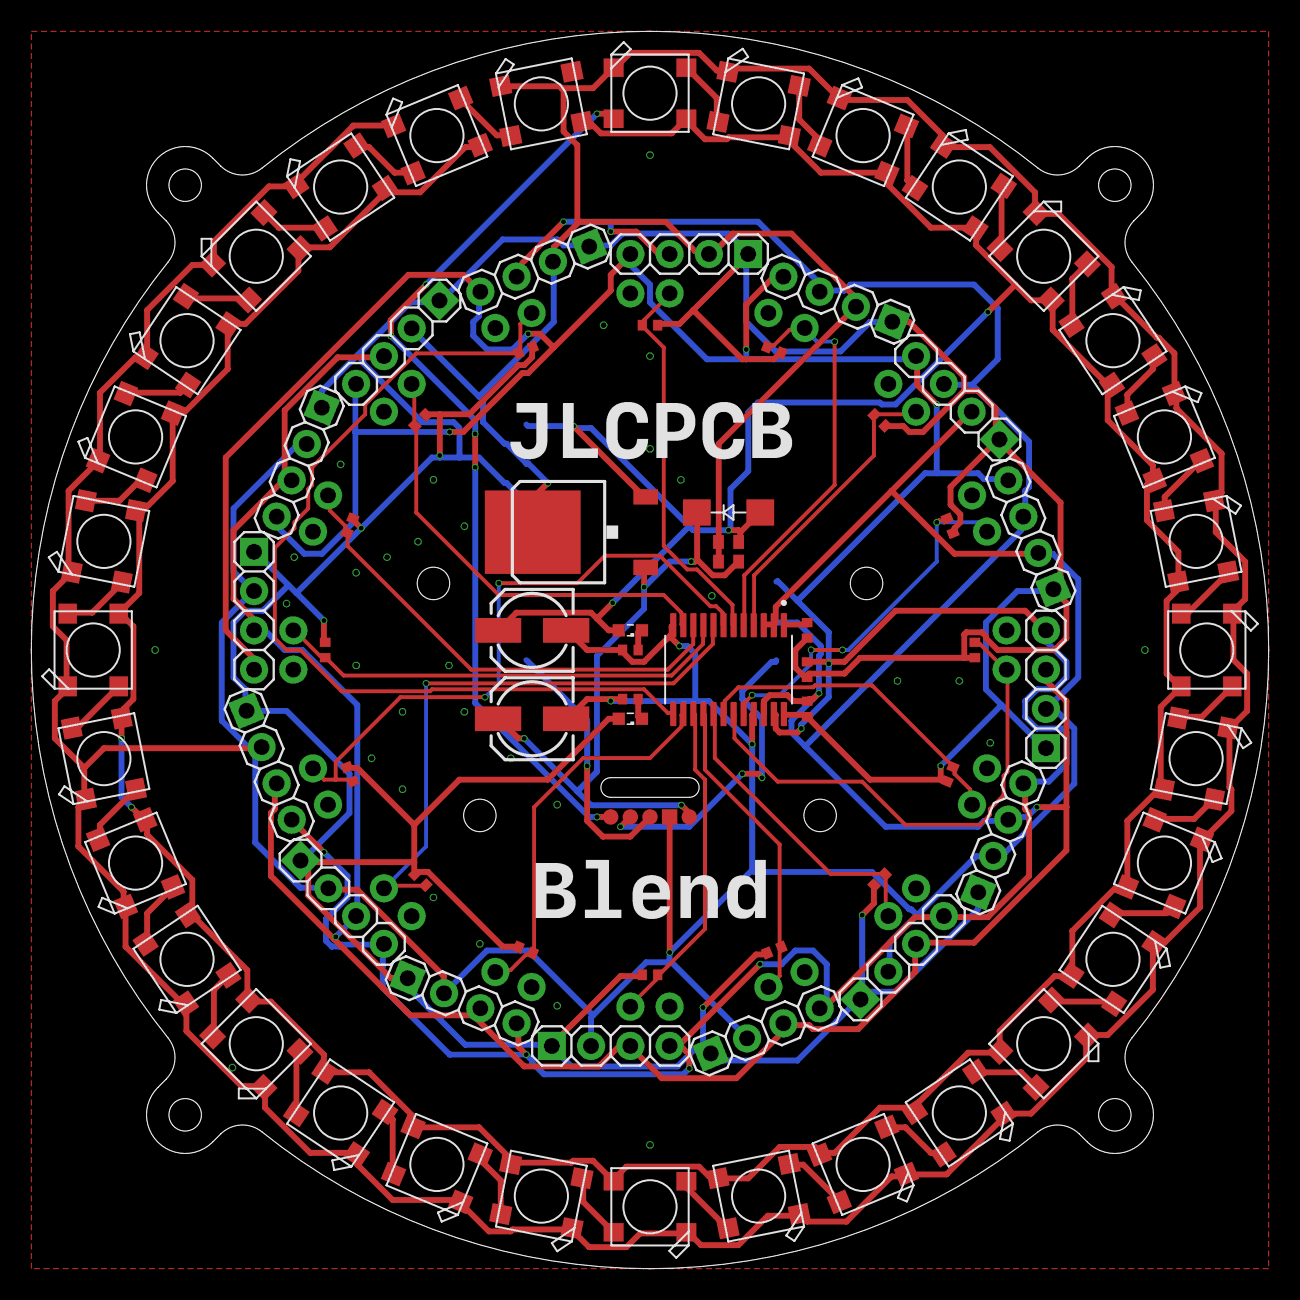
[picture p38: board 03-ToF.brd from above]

Board: 2 copper layers, 80.0 x 80.0 mm, 84 parts (1 on the bottom side), 59 nets.

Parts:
C1: 0.1μ; C0402
C2: 1μ; C0402
C3, C4: 100μ; 153CLV-0505
D1: 1N4007; SMA-DO214AC
LED1, LED2, LED3, LED4, LED5, LED6, LED7, LED8, LED9, LED10, LED11, LED12, LED13, LED14, LED15, LED16, LED17, LED18, LED19, LED20, LED21, LED22, LED23, LED24, LED25, LED26, LED27, LED28, LED29, LED30, LED31, LED32: WS2812B_5050N; WS2812B-NARROW
LED40, LED41: BLUE; SML0603
R1, R2, R5, R6, R7, R8, R9, R10, R11, R12, R13, R14, R15, R16, R17, R18, R19, R20, R21: 10k; R0402
R3, R4: 1k; R0402
REG1: NJM7805; MYPARTS_D-PAK_TO252AA
TP1, TP3, TP4, TP5: PTR1TP10R; TP10R
TP2: PTR1TP10SQ; TP10SQ
U1: MOUDLE14P-2.54-21X17.8MM
U2: PCA9555PW,112; SOP65P640X110-24N
VL1, VL2, VL3, VL4, VL5, VL6, VL7, VL8, VL9, VL10, VL11, VL12, VL13, VL14, VL15, VL16: VL53L0X; 1X04

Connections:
+3V3: LED41.A, R1.2, R2.2, R5.2, R6.1, R7.1, R8.1, R9.1, R10.1, R11.1, R12.1, R13.1, R14.1, R15.1, R16.1, R17.1, R18.1, R19.1, R20.1, R21.1, U1.12, U2.24, VL1.VIN, VL2.VIN, VL3.VIN, VL4.VIN, VL5.VIN, VL6.VIN, VL7.VIN, VL8.VIN, VL9.VIN, VL10.VIN, VL11.VIN, VL12.VIN, VL13.VIN, VL14.VIN, VL15.VIN, VL16.VIN
+5V: C1.1, C3.+, D1.A, LED1.1-VDD, LED2.1-VDD, LED3.1-VDD, LED4.1-VDD, LED5.1-VDD, LED6.1-VDD, LED7.1-VDD, LED8.1-VDD, LED9.1-VDD, LED10.1-VDD, LED11.1-VDD, LED12.1-VDD, LED13.1-VDD, LED14.1-VDD, LED15.1-VDD, LED16.1-VDD, LED17.1-VDD, LED18.1-VDD, LED19.1-VDD, LED20.1-VDD, LED21.1-VDD, LED22.1-VDD, LED23.1-VDD, LED24.1-VDD, LED25.1-VDD, LED26.1-VDD, LED27.1-VDD, LED28.1-VDD, LED29.1-VDD, LED30.1-VDD, LED31.1-VDD, LED32.1-VDD, LED40.A, REG1.3, U1.14
GND: C1.2, C2.2, C3.-, C4.-, LED1.3-GND, LED2.3-GND, LED3.3-GND, LED4.3-GND, LED5.3-GND, LED6.3-GND, LED7.3-GND, LED8.3-GND, LED9.3-GND, LED10.3-GND, LED11.3-GND, LED12.3-GND, LED13.3-GND, LED14.3-GND, LED15.3-GND, LED16.3-GND, LED17.3-GND, LED18.3-GND, LED19.3-GND, LED20.3-GND, LED21.3-GND, LED22.3-GND, LED23.3-GND, LED24.3-GND, LED25.3-GND, LED26.3-GND, LED27.3-GND, LED28.3-GND, LED29.3-GND, LED30.3-GND, LED31.3-GND, LED32.3-GND, R3.2, R4.2, REG1.4, TP2.TP, U1.13, U2.2, U2.3, U2.12, U2.21, VL1.GND, VL2.GND, VL3.GND, VL4.GND, VL5.GND, VL6.GND, VL7.GND, VL8.GND, VL9.GND, VL10.GND, VL11.GND, VL12.GND, VL13.GND, VL14.GND, VL15.GND, VL16.GND
LED_SIG: LED1.4-DIN, TP5.TP
unnamed: LED1.2-DOUT, LED2.4-DIN
unnamed: LED2.2-DOUT, LED3.4-DIN
unnamed: LED3.2-DOUT, LED4.4-DIN
unnamed: LED4.2-DOUT, LED5.4-DIN
unnamed: LED5.2-DOUT, LED6.4-DIN
unnamed: LED6.2-DOUT, LED7.4-DIN
unnamed: LED7.2-DOUT, LED8.4-DIN
unnamed: LED8.2-DOUT, LED9.4-DIN
unnamed: LED10.2-DOUT, LED11.4-DIN
unnamed: LED11.2-DOUT, LED12.4-DIN
unnamed: LED12.2-DOUT, LED13.4-DIN
unnamed: LED13.2-DOUT, LED14.4-DIN
unnamed: LED14.2-DOUT, LED15.4-DIN
unnamed: LED15.2-DOUT, LED16.4-DIN
unnamed: LED16.2-DOUT, LED17.4-DIN
unnamed: LED17.2-DOUT, LED18.4-DIN
unnamed: LED19.2-DOUT, LED20.4-DIN
unnamed: LED20.2-DOUT, LED21.4-DIN
unnamed: LED21.2-DOUT, LED22.4-DIN
unnamed: LED22.2-DOUT, LED23.4-DIN
unnamed: LED23.2-DOUT, LED24.4-DIN
unnamed: LED24.2-DOUT, LED25.4-DIN
unnamed: LED40.C, R3.1
unnamed: LED41.C, R4.1
unnamed: R5.1, U2.1
unnamed: LED25.2-DOUT, LED26.4-DIN
unnamed: LED26.2-DOUT, LED27.4-DIN
unnamed: LED9.2-DOUT, LED10.4-DIN
unnamed: LED28.2-DOUT, LED29.4-DIN
unnamed: LED29.2-DOUT, LED30.4-DIN
unnamed: LED30.2-DOUT, LED31.4-DIN
unnamed: LED31.2-DOUT, LED32.4-DIN
unnamed: LED18.2-DOUT, LED19.4-DIN
unnamed: LED27.2-DOUT, LED28.4-DIN
RX: TP3.TP, U1.8
SCL: R2.1, U1.6, U2.22, VL1.SCL, VL2.SCL, VL3.SCL, VL4.SCL, VL5.SCL, VL6.SCL, VL7.SCL, VL8.SCL, VL9.SCL, VL10.SCL, VL11.SCL, VL12.SCL, VL13.SCL, VL14.SCL, VL15.SCL, VL16.SCL
SDA: R1.1, U1.5, U2.23, VL1.SDA, VL2.SDA, VL3.SDA, VL4.SDA, VL5.SDA, VL6.SDA, VL7.SDA, VL8.SDA, VL9.SDA, VL10.SDA, VL11.SDA, VL12.SDA, VL13.SDA, VL14.SDA, VL15.SDA, VL16.SDA
TX: TP4.TP, U1.7
VDD: C2.1, C4.+, D1.K, REG1.1, TP1.TP
X1: R6.2, U2.6, VL1.X
X2: R7.2, U2.5, VL2.X
X3: R8.2, U2.4, VL3.X
X4: R9.2, U2.20, VL4.X
X5: R10.2, U2.19, VL5.X
X6: R11.2, U2.18, VL6.X
X7: R12.2, U2.17, VL7.X
X8: R13.2, U2.16, VL8.X
X9: R14.2, U2.15, VL9.X
X10: R15.2, U2.14, VL10.X
X11: R16.2, U2.8, VL11.X
X12: R17.2, U2.7, VL12.X
X13: R18.2, U2.9, VL13.X
X14: R19.2, U2.10, VL14.X
X15: R20.2, U2.11, VL15.X
X16: R21.2, U2.13, VL16.X

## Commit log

2023-05-21 基板類全部
    [001-top.brd, 001-top.sch, 01-Futa-B-x10.stl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]
2023-05-21 ToFレイアウト完了
    [001-top.brd, 03-ToF.brd, 03-ToF.sch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]
2023-05-21 配置微調整
    [03-ToF.brd, 03-ToF.sch]
2023-05-22 電源基板完成
    [002-main.brd, 002-main.sch, 003-UI.dxf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]
2023-05-25 main配置完了
    [01-main.brd, 02-ui.brd, 02-ui_top_bom.csv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]
2023-05-25 メイン配線完了
    [01-main.brd]
2023-05-30 配置完了
    [01-main.brd, 01-main.sch, 04-bottom.brd]
2023-05-30 人生楽ありゃ苦もあるさ
    [04-bottom.brd, 04-bottom.sch]
2023-05-30 にゅーぷるあっぷ
    [04-bottom.brd, 04-bottom.sch]
2023-05-30 配線完了！！
    [04-bottom.brd]
2023-05-30 Revert "ねこ"
    This reverts commit a85c6a9ac54e5e413855fdb3eef226a7b30d2926.
2023-05-30 Revert "配線完了！！"
    This reverts commit 358a7b28429e96d6d805ade8accdc2bc4b7907af.
    [04-bottom.brd]
2023-05-30 今度こそ配置完了？
    [04-bottom.brd, 04-bottom.sch]
2023-05-31 メイン配置おわ
    [01-main.brd, 01-main.sch]
2023-05-31 ちびちび
    [01-main.brd]
2023-05-31 wet cat
    [01-main.brd, 01-main.sch]
2023-06-02 書き出し
    [01-main.brd, 01-main_top_bom.csv, 04-manta.sch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]

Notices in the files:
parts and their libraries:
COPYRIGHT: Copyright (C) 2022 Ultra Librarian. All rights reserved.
